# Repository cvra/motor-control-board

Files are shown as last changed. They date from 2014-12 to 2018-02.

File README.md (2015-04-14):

CVRA DC-Motor Controller
========================

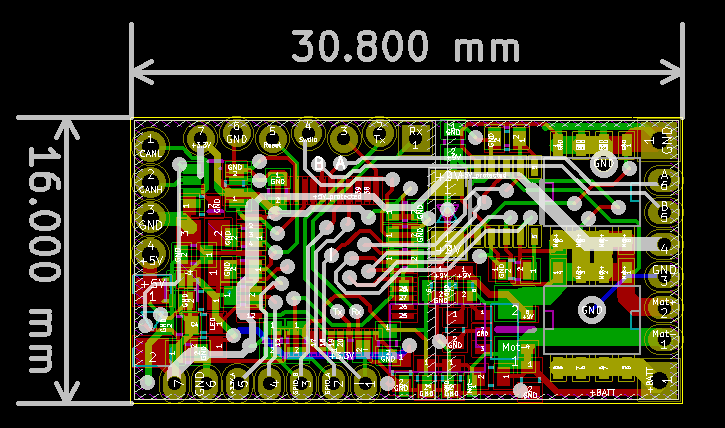
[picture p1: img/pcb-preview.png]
pcb


Features:
---------

 - CAN interface
 - DC motor control with current sensing
 - Quadrature encoder interface for motor (5V tolerant)
 - Secondary quadrature encoder interface (5V tolerant) (eg. for separate odometry wheels)
 - Analog input for RC-servo control
 - Runs on 3 or 4 cell LiPo batteries

License
-------
This project is released under the Creative Commons CC-BY-SA-4.0 license.
See http://creativecommons.org/licenses/by-sa/4.0/ for details.

Assembly
--------

# Applying solder paste

 - This needs 2 persons.
 - Solder paste and stencil need to be _cold_ (couple of minutes in the fridge)
 - Use the 3D printed frames. Stick them to the table with double sided tape
    and stick the PCB to the frame with small pieces of double sided tape.
    If you don't do this, the PCB will stick to the sencil when you try to remove it.
 - To remove the stencil, rotate it around one of the short edges, to pull it
   as perpendicular as possible with the least amount of shaking.
 - Move the PCB with the applied solder paste to a frame without double sided
   tape before assembling the parts, because they would probably flick off.
 - Check the footprints with the smallest pitch under the microscope for bad
   alignment and if the brim is nice (if it isn't, the paste was probably too warm).

# Assembling the parts
 - Remove the solder paste on the NC pad of the voltage regulator with the wrong
   footprint.
 - Use the vacuum pump for larger parts and tweezers for smaller ones.

# Baking

 - Preheat the frame made out of plaster to >200°C, else it won't reflow!
 - Move the PCB to the plaster frame.
 - Put the frame and the thermal probe in the furnace. Take care that you don't
   accidentally move any parts by touching them with the probe.
 - Heat until the solder paste starts to liquidify (shouldn't be more than
   ~230°C; never go higher than 250°C).
 - Keep the peak temperature for about a minute.
 - Open the furnace door a little bit to slowly cool down the PCBs.
 - Don't remove the PCB from the furnace before it's colder than ~70°C.

# Flashing and testing

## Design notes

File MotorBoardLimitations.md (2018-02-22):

# Motor Board Limitations

These limitations apply to REV A of the board.

## Driver input signals don't respect absolute max. rating when powered off
The driver input signals must not exceed its supply voltage. When the main
power bus is unpowered the STM32 drive signals are still active at 3.3V level.
The workaround is to configure the driver signals to open drain output with
internal pullup on the STM32 side. This induces a small lag for the rising
edge of the signal.

## Motor output floating on power loss (should be shorted to gnd)
When the main power supply is cut (for example in case of an emergency stop)
the mosfet driver is unpowered and the all mosfets are open. The motor coil
current and the motor generator voltage are injected in the (now unpowered)
power supply bus trough the mosfet diodes. This can cause voltage spikes
on the power bus.
Also it would be preferable to to brake the motor by shorting it case of
in an emergency stop condition.

## Common mode voltage steps on the sense resistor cause disturbances in the current sense amplifier output
A common mode voltage step on the driver causes a pulse on the INA282 amplifier
that lasts for about 10us. (see fig 3 - 6 page 6 of the datasheet)
This makes PWM operation of 25kHz impossible on the sense resistor side.
The workaround is to use the half bridge with the sense resistor in a static
'direction' mode and the other half bridge in PWM voltage mode. Unfortunately
the mosfet driver can't drive a 100% high signal because of the high side gate
driver that recharges its drive capacitor during the low period. To recharge
the high side drive capacitor a low switch during 10us has to be inserted every
2ms.
These recharging cycles as well as changes of drive direction still cause common mode
voltage steps on the sense resistor. The effect of this on the current measurement
resolution still has to be determined.

## Audible noise caused by recharge cycles at 500Hz
The current workaround for the common mode steps on the sense resistor uses
recharge cycles for the drive capacitor every 2ms (see above).
This causes an audible 500Hz tone.
(This can be mitigated by choosing the recharge period randomly between 1ms and
2ms which spreads the noise in the spectrum between 500Hz and 1kHz which is
less displeasing.)

## TPS71501 voltage regulator issues

The TPS71501 voltage regulator (IC1) gets damaged after a short time.
It can be removed and replaced by 560 Ohm resistor connecting pads 4 and 5.

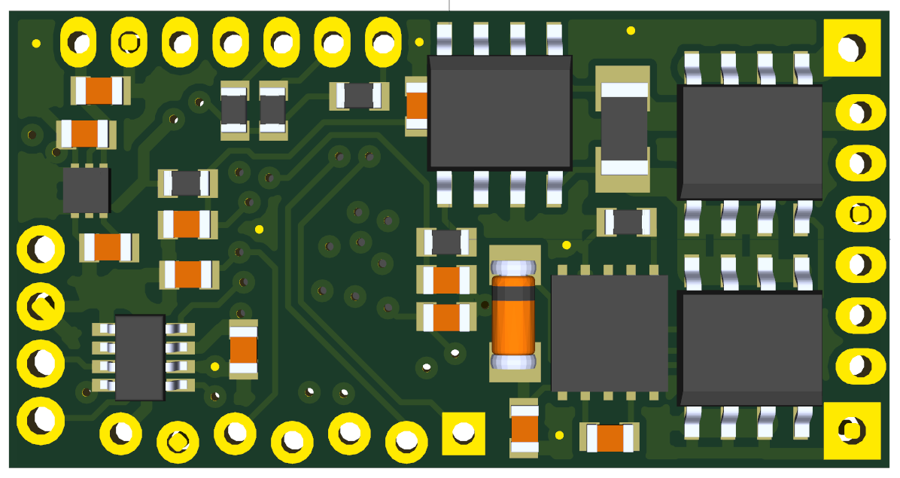
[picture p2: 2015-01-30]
img/3d-motor-back.png

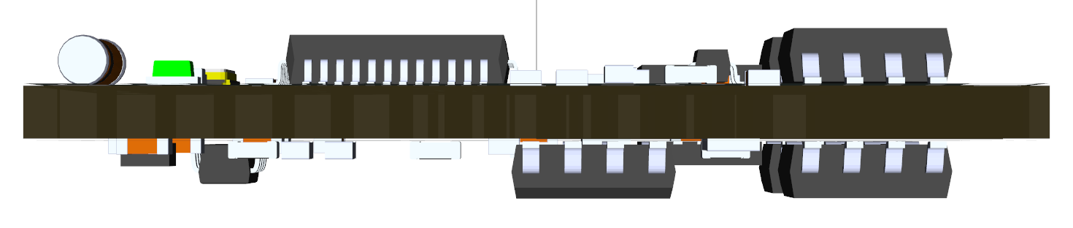
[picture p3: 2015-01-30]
img/3d-motor-side.png

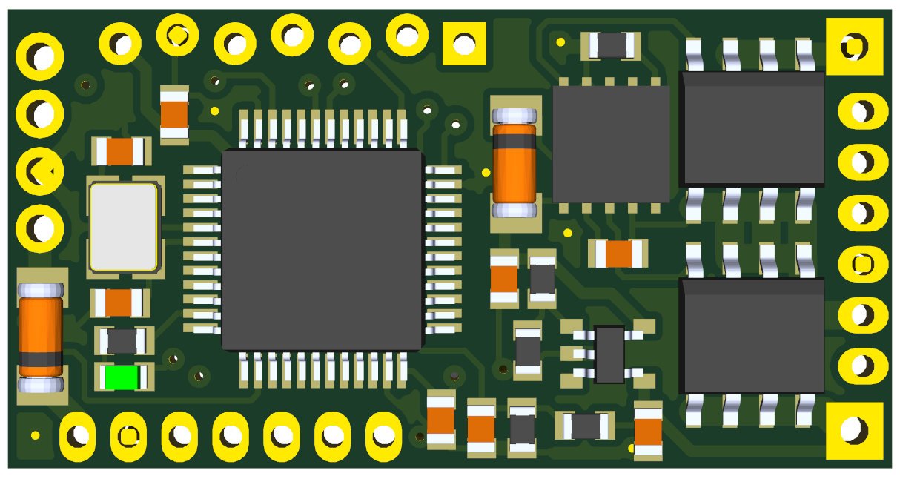
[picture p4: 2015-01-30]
img/3d-motor-front.png

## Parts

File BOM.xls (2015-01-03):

Référence | Boitier | Quantité | Désignation | Fournisseur et réf.
C10,C18 | _0603 | 2 | 10nF/50V/X7R | 399-1092-1-ND
C11,C12 | _0603 | 2 | 10pF/50V/COG | 445-5048-1-ND
C16,C14 | _0603 | 2 | 47nF/50V/X7R | 1276-1063-1-ND
C17,C8 | _0603 | 2 | 1uF/25V/X7R | 1276-1184-1-ND
C3 | _0603 | 1 | 4.7uF/10V/X5R | 1276-1044-1-ND
C4 | _0603 | 1 | 470n/50V/X7R | 445-5952-1-ND
C7,C9,C6,C13,C5,C1,C2,C15,C19 | _0603 | 9 | 100nF/50V/X7R | 445-1314-1-ND
D1 | CVRA-SOD80C | 1 | LL103C | LL103C-GS08CT-ND
D2 | _0603 | 1 | LED verte | 754-1121-1-ND
D3,D4 | CVRA-SOD80C | 2 | BAV102 | BAV102-GS08GICT-ND
IC1 | CVRA-SOT23-5 | 1 | TPS71501 | 296-12957-1-ND
IC2 | CVRA-PWSON-N6 | 1 | TLV710 | 296-29058-1-ND
IC3 | _SOT23-8 | 1 | MAX3051 | MAX3051EKA+TCT-ND
IC4,IC5 | PSONL10 | 2 | LM5106 | LM5106SD/NOPBCT-ND
IC6 | CVRA-SO8E | 1 | INA282 | 296-27820-1-ND
L1 | _0603 | 1 | 100uH | 445-6150-1-ND
P1 | pin4_can_connector | 0 | Bus2
P2 | ribbon_cable_6pin | 0 | MOTOR
P3 | ribbon_cable_7pin | 0 | GPIO
P5 | _Pin2mm_7z | 0 | DBG
P6,P4 | PWR_Conn | 0 | CONN_1
Q1,Q2,Q4,Q3 | CVRA-SO8E | 4 | IRF8721 | IRF8721TRPBFCT-ND
R1 | _0603 | 1 | 5.6M | 541-5.60MHCT-ND
R10 | CVRA-1206-1 | 1 | 0.01R | 985-1547-1-ND
R13 | _0603 | 1 | 18k | 541-18.0KHCT-ND
R2 | _0603 | 1 | 910k | P910KHCT-ND
R3,R5,R6 | _0603 | 3 | 10k | 541-10.0KHCT-ND
R4 | _0603 | 1 | 22R | 541-22.0HCT-ND
R8,R11,R12 | _0603 | 3 | 100k | 541-100KHCT-ND
R9 | _0603 | 1 | 330R | 541-330HCT-ND
U1 | _LQFP48 | 1 | STM32F303CCT6 | 497-13318-ND
X1 | _TSX-3225-SMD-XTAL | 1 | 16MHz | SER3628CT-ND

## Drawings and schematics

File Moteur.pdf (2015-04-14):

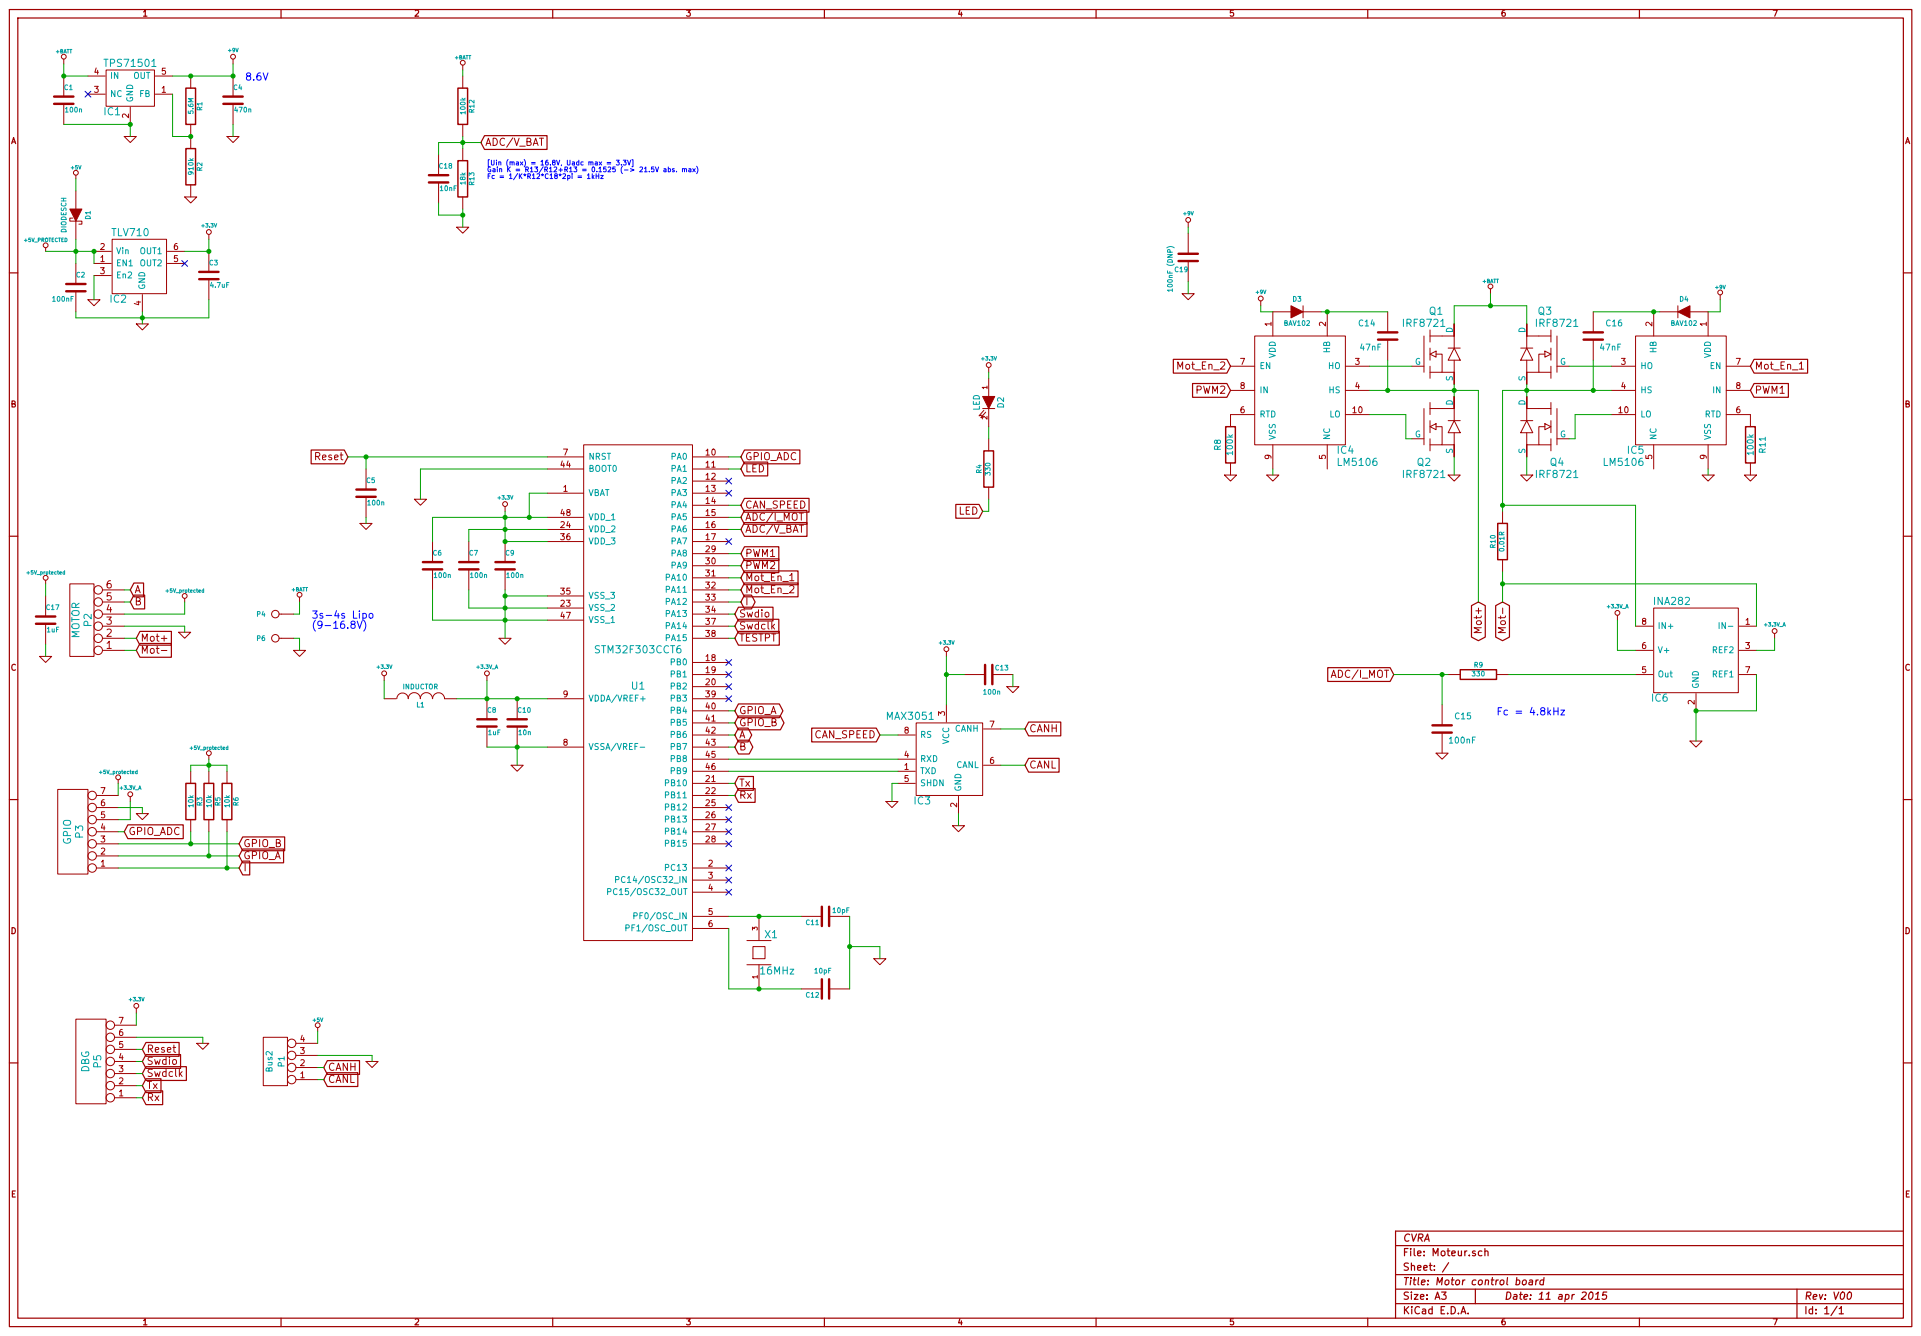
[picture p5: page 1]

[Uin (max) = 16.8V, Uadc max = 3.3V] Gain K = R13/R12+R13 = 0.1525 (-> 21.5V abs. max) Fc = 1/K*R12*C18*2pi = 1kHz 3s-4s Lipo

3 RXD 4 SHDN 5 CANL 6 CANH 7 RS 8

CVRA
Id: 1/1 Title: Motor control board File: Moteur.sch Sheet: /

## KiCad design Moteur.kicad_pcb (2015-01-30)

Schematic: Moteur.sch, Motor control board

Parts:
C1, C5, C6, C7, C9, C13: 100n
C2: 100nF
C3: 4.7uF
C4: 470n
C8, C17: 1uF
C10: 10n
C11, C12: 10pF
C14, C16: 47nF; SM1206
C15: 100nF; SM1206
C18: 10nF
C19: 100nF (DNP)
D1: DIODESCH
D2: LED
D3, D4: BAV102; diode-1-SOD80C
IC1: TPS71501
IC2: TLV710
IC3: MAX3051
IC4, IC5: LM5106
IC6: INA282
L1: INDUCTOR
P1: Bus2
P2: MOTOR
P3: GPIO
P4, P6: CONN_1
P5: DBG
Q1, Q2, Q3, Q4: IRF8721; transistor-power-SOT669
R1: 5.6M
R2: 910k
R3, R5, R6: 10k
R4: 22
R8, R11: 100k; SM0805
R9: 330
R10: 0.01R
R12: 100k
R13: 18k
U1: STM32F303CCT6; MODULE
X1: 16MHz

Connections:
+3.3V: C3.1, C6.1, C7.1, C9.1, C13.2, D2.1 (A), IC2.6 (OUT1), IC3.3 (VCC), L1.1, P5.7, U1.1 (VBAT), U1.24 (VDD_2), U1.36 (VDD_3), U1.48 (VDD_1)
+3.3V_A: C8.1, C10.1, IC6.3 (REF2), IC6.6 (V+), L1.2, P3.5, U1.9 (VDDA/VREF+)
+5V: D1.1 (A), P1.4
+9V: C4.1, C19.2, D3.1 (A), D4.1 (A), IC1.5 (OUT), IC4.1 (VDD), IC5.1 (VDD), R1.1
+BATT: C1.1, IC1.4 (IN), P4.1, Q1.5 (D), Q1.6, Q1.7, Q1.8, Q3.5 (D), Q3.6, Q3.7, Q3.8, R12.1
A: P2.6, U1.42 (PB6)
ADC/I_MOT: C15.1, R9.1, U1.15 (PA5)
ADC/V_BAT: C18.1, R12.2, R13.1, U1.16 (PA6)
B: P2.5, U1.43 (PB7)
CANH: IC3.7 (CANH), P1.2
CANL: IC3.6 (CANL), P1.1
CAN_SPEED: IC3.8 (RS), U1.14 (PA4)
GND: C1.2, C2.2, C3.2, C4.2, C5.2, C6.2, C7.2, C8.2, C9.2, C10.2, C11.2, C12.2, C13.1, C15.2, C17.2, C18.2, C19.1, IC1.2 (GND), IC2.3 (En2), IC2.4 (GND), IC3.2 (GND), IC3.5 (SHDN), IC4.9 (VSS), IC5.9 (VSS), IC6.2 (GND), IC6.7 (REF1), P1.3, P2.3, P3.6, P5.6, P6.1, Q2.1 (S), Q2.2, Q2.3, Q4.1 (S), Q4.2, Q4.3, R2.2, R8.2, R11.2, R13.2, U1.8 (VSSA/VREF-), U1.23 (VSS_2), U1.35 (VSS_3), U1.44 (BOOT0), U1.47 (VSS_1)
GPIO_A: P3.2, R5.2, U1.40 (PB4)
GPIO_ADC: P3.4, U1.10 (PA0)
GPIO_B: P3.3, R3.2, U1.41 (PB5)
I: P3.1, R6.2, U1.33 (PA12)
LED: R4.1, U1.11 (PA1)
Mot+: C14.2, IC4.4 (HS), P2.2, Q1.1 (S), Q1.2, Q1.3, Q2.5 (D), Q2.6, Q2.7, Q2.8
Mot-: IC6.1 (IN-), P2.1, R10.1
Mot_En_1: IC5.7 (EN), U1.31 (PA10)
Mot_En_2: IC4.7 (EN), U1.32 (PA11)
unnamed: IC6.5 (Out), R9.2
unnamed: D2.2 (K), R4.2
unnamed: IC1.1 (FB), R1.2, R2.1
unnamed: IC3.1 (TXD), U1.46 (PB9)
unnamed: IC3.4 (RXD), U1.45 (PB8)
unnamed: IC4.10 (LO), Q2.4 (G)
unnamed: IC4.3 (HO), Q1.4 (G)
unnamed: IC5.10 (LO), Q4.4 (G)
unnamed: IC5.3 (HO), Q3.4 (G)
unnamed: C16.2, IC5.4 (HS), IC6.8 (IN+), Q3.1 (S), Q3.2, Q3.3, Q4.5 (D), Q4.6, Q4.7, Q4.8, R10.2
unnamed: IC4.6 (RTD), R8.1
unnamed: C14.1, D3.2 (K), IC4.2 (HB)
unnamed: C16.1, D4.2 (K), IC5.2 (HB)
unnamed: IC5.6 (RTD), R11.1
unnamed: C11.1, U1.5 (PF0/OSC_IN), X1.3
unnamed: C12.1, U1.6 (PF1/OSC_OUT), X1.1
PWM1: IC5.8 (IN), U1.29 (PA8)
PWM2: IC4.8 (IN), U1.30 (PA9)
Reset: C5.1, P5.5, U1.7 (NRST)
Rx: P5.1, U1.22 (PB11)
Swdclk: P5.3, U1.37 (PA14)
Swdio: P5.4, U1.34 (PA13)
Tx: P5.2, U1.21 (PB10)

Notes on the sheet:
Fc = 4.8kHz
[Uin (max) = 16.8V, Uadc max = 3.3V] Gain K = R13/R12+R13 = 0.1525 (-> 21.5V abs. max) Fc = 1/K*R12*C18*2pi = 1kHz
3s-4s Lipo (9-16.8V)
8.6V

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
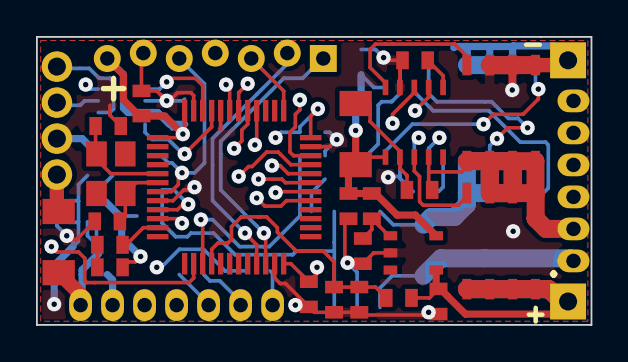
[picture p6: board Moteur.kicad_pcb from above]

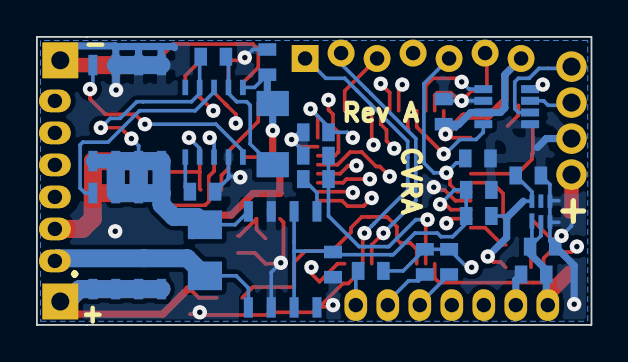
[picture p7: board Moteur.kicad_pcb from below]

Board: 4 copper layers, 30.8 x 16.0 mm, 54 parts (26 on the bottom side), 46 nets.

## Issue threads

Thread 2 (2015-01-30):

Fix footprint for TPS71501

antoinealb, 2015-01-30:

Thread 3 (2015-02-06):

Higher PWM frequency limit

antoinealb, 2015-02-06:
The current max PWM frequency is about 2.5 kHz, due to a problem in the current measurement circuit. Having a limit > 20kHz would be nice for noise purposes.

Stapelzeiger, 2015-02-06:
should be fixed now

antoinealb, 2015-02-06:
Could you explain the problem quickly ?

Stapelzeiger, 2015-02-06:
Previously the current sense resistor was connected to one of the mosfet half bridge outputs in series with the dc motor. This caused a problem when this half bridge was active, doing PWM since the common mode voltage of the sense resistor switches between zero and 15V.
The amplifier we are using has a good common voltage rejection, but only statically. For a step in common mode voltage, the output makes a pulse of about 10us length.
(see [Datasheet](www.ti.com/lit/ds/symlink/ina282.pdf) page 6, figure 3-6)
For 25kHz (period of 40us) PWM this disturbance is significant. This is why current sense only worked for low (around 2kHz) frequencies.
Now the sense resistor is in series with the supply (on the high side) and is therefore not exposed to common voltage steps. Using this configuration we'll need to compensate for the fact that during PWM off time, the measured current is zero even though the current in the motor stays (almost) constant.

SyrianSpock, 2015-02-06:
There are 3 ways of measuring current in the H-bridge:
* The shunt is wired in series with the motor (rev 1.0) which constrains the op amp to have a high CMRR (Common mode rejection ratio) which it turns out is quite low at inaudible frequencies.
* The shunt is wired between high side (battery) and H-bridge which is the solution proposed to solve this issue,
* The shunt is wired between low side (ground) and H-bridge.

Both last solutions increase ground resistance, but this is negligible since our shunt is 10mOhm. They also don't allow to measure the current continuously since you can't monitor the current that flows from the diode to the motor so you need to compensate for that in the software.

I think the solution proposed is the best that can be done to ensure that the fewest changes to the design so we don't need to spend a lot of time reviewing and we can keep the stencil.

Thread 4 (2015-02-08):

mosfet driver input exceeds absolute maximum ratings

Stapelzeiger, 2015-02-08:
When the 15V power supply is shut off, the inputs of the mosfet driver are still driven by the STM32.

antoinealb, 2015-02-08:
can that lead to MOSFET destruction ?

Le dimanche 8 février 2015, Patrick Spieler <notifications@github.com> a
écrit :

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

Stapelzeiger, 2015-02-08:
no, but it might damage the mosfet driver or the STM32.
Currently our workaround is to use open-drain output & pullup on the STM32.

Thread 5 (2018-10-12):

on board daisy chain CAN connectors

antoinealb, 2018-10-12:
Currently the CAN connections are done through a "Y" wire. That was a design mistake on this board and all later CVRA boards have two on board connectors and are then daisy chained using straight male to male cables. The second revision should have that.

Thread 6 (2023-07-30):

Available online to buy and protptype?

SoumyaMaitra, 2023-07-30:
Guys this is a very nice development. We are working on a humanoid which uses small but torque 40kgcm servos Savox 1270TG.
We wanted to use your board to control it via CAN with current-based torque control and position control, PID etc. We want to use a 14but AMS magnetic encoder to sense the horn position.  Can we use your board on it and for testing do you sell the developed tested board?
We dont have deep embedded experience so will you be able to take a development work?

antoinealb, 2023-07-31:
Hi, we don't have it available in an online store but we might be able to sell you one or two that we assembled for our own use, if it helps with your development. I will have to check our inventory. Another option would be to fix the design (there is a small error in the PCB) and have it manufactured by someone.

> We want to use a 14but AMS magnetic encoder to sense the horn position.

We have an extension for this board to do this, if you are interested: https://github.com/cvra/angle-sensor-board. We don't have firmware for reading the sensor yet, but it could be developped.

> We dont have deep embedded experience so will you be able to take a development work?

I asked who in our team would have the time to do it, I will get back to you in a few days.

Lu-ni, 2023-08-02:
Hey @SoumyaMaitra,

It's awesome to hear about your project - a humanoid with Savox 1270TG servos sounds like some seriously cool tech!

After a chat with the team, we're stoked to let you know our board is a pretty good match for what you're looking to do - it can handle current-based torque control, position control, and PID, and should play nice with your 14bit AMS magnetic encoder for horn position sensing. For more info about what our tech can do, check out our [Motor Board](https://cvra.ch/robot-software/can/motor/) and [CAN Ecosystem](https://cvra.ch/robot-software/can/intro/) pages.

Regarding getting your hands on a developed, tested board for testing, we can absolutely sort that out. We'll just need to discuss some of the specifics like timelines, costs, and how we'll get it to you.

To move things forward, it'd probably be best if we switch over to email for the details. You can reach me at lucas.nicollier[at]gmail.com.

Catch you soon,

Lucas

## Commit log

2014-10-31 add kicad lib submodule
2014-10-31 add all libs
    [Moteur.sch]
2014-10-31 add correct stm32 symbol
    [Moteur.sch]
2014-11-05 design review
    [Moteur.sch]
2014-11-05 update library path
    [Moteur.sch]
2014-11-05 Add something useless
    [Moteur.sch]
2014-11-05 remove something useless
    [Moteur.sch]
2014-11-05 update current measurement filter, fix connection CAN termination resistor
    [Moteur.sch]
2014-11-05 power supply minor fixes
    [Moteur.sch]
2014-11-09 Schéma Complet
    [Moteur.sch]
2014-11-12 Couche PCB Définie
    [Moteur.kicad_pcb]
2014-11-13 minor schematic fixes, start assigning footprints
    [Moteur.sch]
2014-11-13 footprints assignment
2014-11-13 connect encoders to diode protected 5V
    [Moteur.sch]
2014-11-13 add V_Bat resistive divider for ADC
    [Moteur.sch]
2014-11-13 Fix 5V protected symbol name
    Apparently KiCAD has case sensitive symbol names... nice
    [Moteur.sch]
2014-11-15 Add Diode
    [Moteur.sch]
2014-11-16 Set footprint for TLV710 and LM5106 Corrected footprint for shunt resistor
2014-11-22 Update footprint link, disperse component on PCB and add pcb size
    [Moteur.kicad_pcb, Moteur.sch]
2014-11-23 Add board outline and placed power stage
    [Moteur.kicad_pcb]
2014-11-23 Placement driver can
    [Moteur.kicad_pcb]
2014-11-26 fix labels, pinout
    [Moteur.sch]
2014-11-26 final schematic review, component placement
    [Moteur.kicad_pcb, Moteur.sch]
2014-11-27 component placement
    [Moteur.kicad_pcb]
2014-11-28 add GND to GPIO connector, exchange CANL,CANH
    [Moteur.sch]
2014-11-28 optimize placement
    [Moteur.kicad_pcb]
2014-11-28 add new gpio connector with gnd
    [Moteur.kicad_pcb]
2014-12-02 start routing
    [Moteur.kicad_pcb]
2014-12-03 exchange shunt resistance pins
    [Moteur.sch]
2014-12-03 routing, exchanged shunt resistor pins
    [Moteur.kicad_pcb]
2014-12-03 routing (power)
    [Moteur.kicad_pcb]
2014-12-05 routing, almost done
    [Moteur.kicad_pcb]
2014-12-06 routing, changed connectors
    [Moteur.kicad_pcb, Moteur.sch]
2014-12-06 update debug connector footprint
    [Moteur.kicad_pcb]
2014-12-08 update connector, thermal for connectors
    [Moteur.kicad_pcb]
2014-12-08 Battery gnd thermal
    [Moteur.kicad_pcb]
2014-12-08 gnd via
    [Moteur.kicad_pcb]
2014-12-08 add schematic pdf
2014-12-10 Gerber fabrication output.
    [Moteur.GBL, Moteur.GBO, Moteur.GBP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]
2014-12-10 readme & pcb preview
2015-01-03 resistive divider values & schematic annotations
    [Moteur.sch]
2015-01-03 add BOM
    [BOM.xls]
2015-01-30 Place 3d models on PCB and export in VRML format
    [Moteur.kicad_pcb]
2015-01-30 Revert "Place 3d models on PCB and export in VRML format"
    This reverts commit 3c79a8abd9414d5cc485e12aba148d6700e70ad2.
    [Moteur.kicad_pcb]
2015-01-30 Fixing some 3d model issues
    [Moteur.kicad_pcb]
2015-02-01 Update 3d model with components on PCB embedded in VRML
2015-02-01 Update VRML 3d model of PCB
2015-02-06 remove RGB-led datasheet
2015-04-08 started writing an assembly guide
2015-04-11 correct LED resistor
    [Moteur.sch]
2018-02-22 Document voltage regulator issue
